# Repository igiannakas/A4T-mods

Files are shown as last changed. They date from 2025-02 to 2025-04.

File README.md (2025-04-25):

# WWG2 Mods for the A4T toolhead and filament cutter
This is my collection of mods for the A4T Toolhead (developed by Armchair-Heavy-Industries) cutter developed by SouthAsh1 and WWG2 (Wrist Watch G2) extruder developed by tetsu97 and modified by bythorsthunder to include a dual filament sensor. 

**Project source links below:**
1. https://github.com/Armchair-Heavy-Industries/A4T
2. https://github.com/bythorsthunder/Voron_Mods/tree/main/Wristwatch_G2_Dual_Filament_Sensor
3. https://github.com/SouthAsh1/A4T-AFC

All licenses are carried over from their respective creators. License information available in the links above.



# Modifications overview and rationale:
During my use of the A4T toolhead together with the southash1 developed filament cutter and Wrist Watch G2 extruder I've come across the following areas for improvement:

1. **Filament path diameter:** The WWG2 filament path was hexagonal, which while OK in principle, is "looser" than the latest circular filament path implemented in the G2E extruder by JaredC01. **Specifically the hexagonal path is up to 2.54mm in diameter vs. 2.1mm in the latest G2E extruder release.** This results in the filament path not being as constrained, which resulted in observable deviations in the PA value between G2E and WWG2. A cross sectional image of the revised filament path can be found below:


2. **WWG2 Filament entry point:** The WWG2 mod to include the dual filament sensors results in a **very thin wall between the upper ball bearing and the filament path** and entry point. This results in the filament path deforming when printed. In addition, the filament entry path has a **very shallow taper** where the filament enters the extruder from the top ECAS fitting. This results in slight filament collisions if the filament enters the extruder at a slight angle due to the filament twisting in the feeding tube or curling due to its natural spool curge. **These have been addressed in the modded design by elevating the ECAS mount point by 1mm and agressively tapering the filament entry path.** A cross sectional image of the revised filament entry path can be found below:


3. **WWG2 Filament exit and A4T direct filament entry path:** The dual filament sensor WWG2 had a very small recess to mount a bowden tube to the filament exit point. While this works well for toolheads that have a large bowden section after the extruder, when used in combination with the A4T AFC toolhead cutter, it resulted in **approximately 2-3mm of bowden tube needed to constrain the filament between the extruder and the A4T AFC extruder mount** adaptor. In addition, that bowden tube recess was again resulting in **thin walls on the WWG2** filament path that were deforming after printing. **Both of these have been addressed in the modded design by removing the bowden recess from both the WWG2 and the A4T extruder mount.** That small bowden tube was uncecessary and has been replaced with a coincident filament path, tapered at the entry of the A4T AFC to allow for proper filament guidance.


Please note that the M2 heatset is still needed to guide the filament through to the cutter and is fitted underneath the extruder adaptor filament path, here:


4. **WWG2 M3x20 and M3x25 screws mod:** The stock WWG2 main body requires M3x20 and M3x18 screws. I have discovered that the M3x20 is barely long enough to make it fully through the square nut. Also they do not extend all the way through to the holes underneath the nut, somewhat reducing stability. In this mod, the WWG2 front plate has been modified to allow for the use of M3x20 and M3x25 screws


5. **Reinforced blade holder:** While the stock design works well with PLA and ABS, when cutting fiber reinforced material (eg. PPA CF, PET CF) it tends to crack at infront of the lever bushing. The reinforced blade holder thickens that area allowing for more walls to be extruded, reducing the opportunity for cracks to appear.
 




6. **Updated WWG2 THB mount:** Updated THB mount for the XOL carriage with the rear support screw now able to be used again.


7. **Experimental: Updated cowling with enhanced support for the G2 extruder gearbox:** What I have noticed is that the extruder is now mounted a bit higher up compared to the stock A4T hotend. This allows the WWG2 extruder room to "vibrate" as the extruder rear plate is unsupported vs. the stock A4T where the extruder is supported by the housing of the A4T. I have updated the cowling to extend the rear mounting plate to support the underside of the WWG2 resulting in slightly improved IS results.

 

 

Please note that you will need to use supports in the slicer to print the extended support area. Apologies my CAD skills are not good enough to do this natively! Also as this is experimental, I have ony updated the Revo XOL cowling as that is the one my printer is using!



# Assembly tips
As the filament paths are now tigther than the original designs (2.1mm in diameter) you may need a 2mm drill bit to ream them out slightly if they are too tight for filament to pass through easily.

The **WWG2 extruder has shrinkage compensation for ABS like materials already built in** the base design, from which these mods are derived from. So in theory you shouldnt need to scale the parts.

The **A4T AFC parts do not have shrinkage compensation baked in the CAD**, so you'll need to apply your material shrinkage compensation as per the base design instructions.

Happy printing!

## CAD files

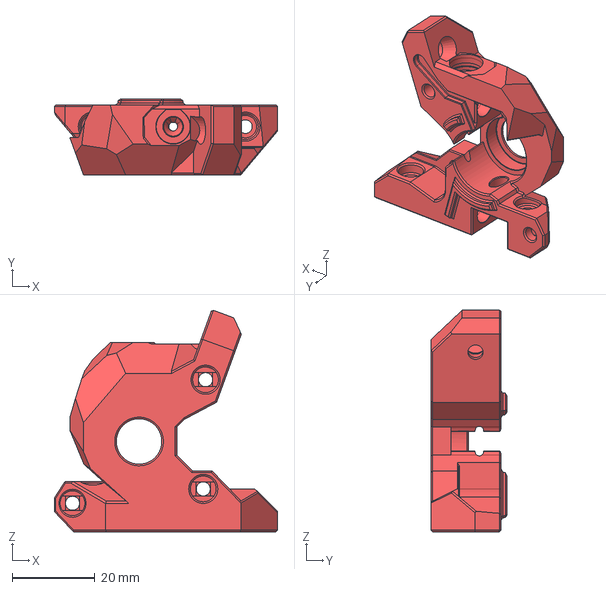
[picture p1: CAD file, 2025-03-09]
WWG2 Dual Filament Sensor/STEP/WWG2_DualFS Main body.step
54.1 x 18.4 x 53.7 mm

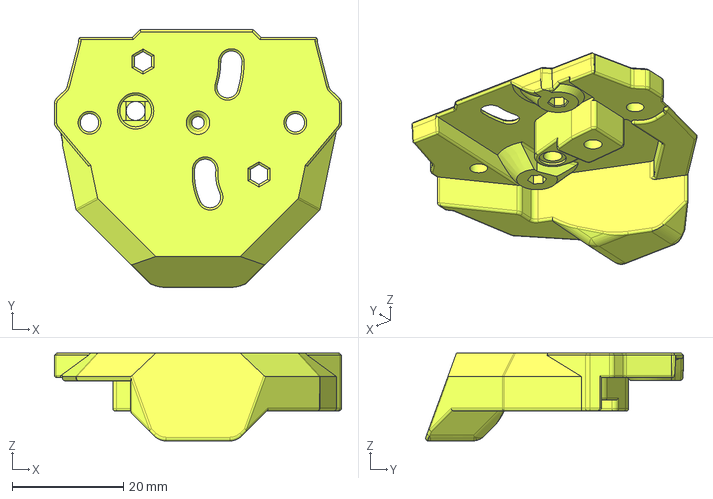
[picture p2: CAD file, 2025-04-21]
A4T - AFC mods/01. Extruder adapter - direct entry path/CAD/Extruder adapter - standard flow - direct entry path.step
51.6 x 46.3 x 15.8 mm

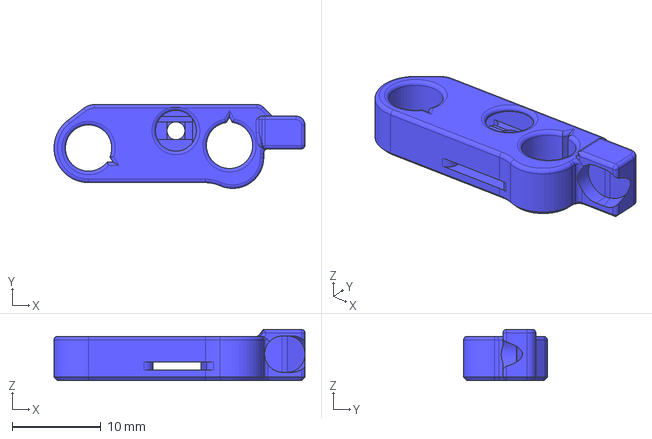
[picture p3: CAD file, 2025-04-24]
A4T - AFC mods/02. Reinforced blade holder/CAD/Blade Holder - reinforced.step
28.3 x 9.45 x 5.80 mm

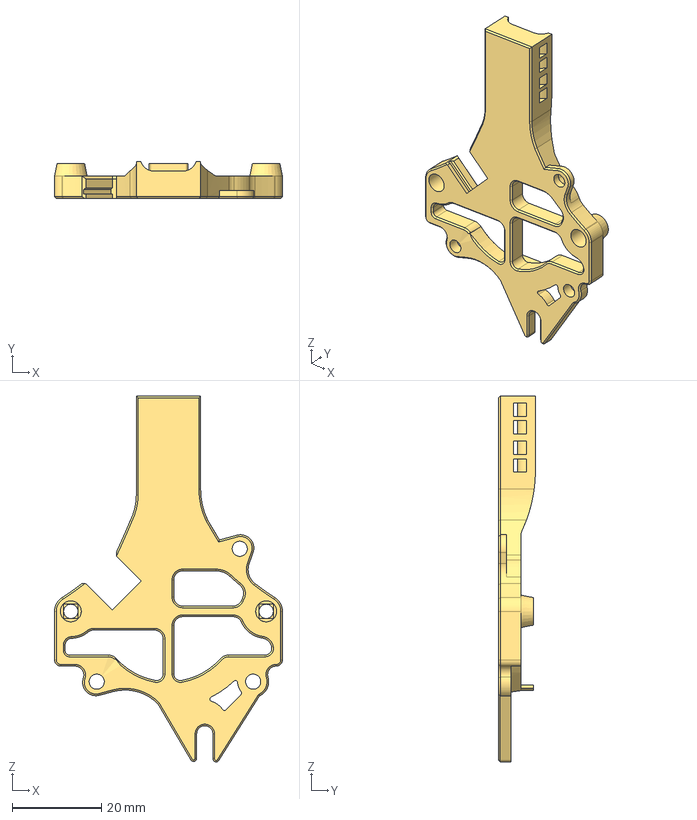
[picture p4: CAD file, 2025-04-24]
A4T - AFC mods/03. WWG2 THB Mount/CAD/THB Mount.step
51.2 x 8.26 x 82.1 mm

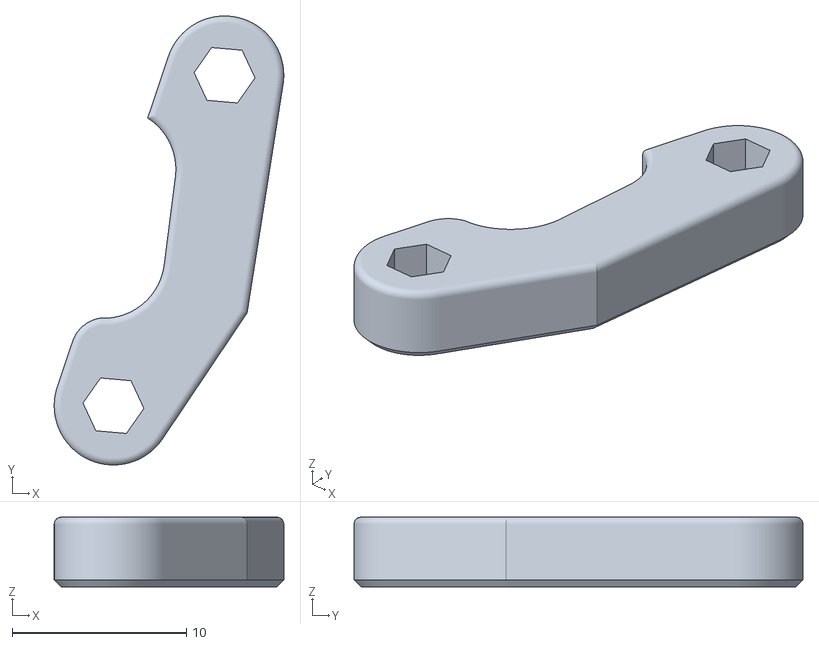
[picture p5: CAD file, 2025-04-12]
A4T - AFC mods/05. Remaining files from source repo/Link.stl
13.2 x 25.8 x 4.00

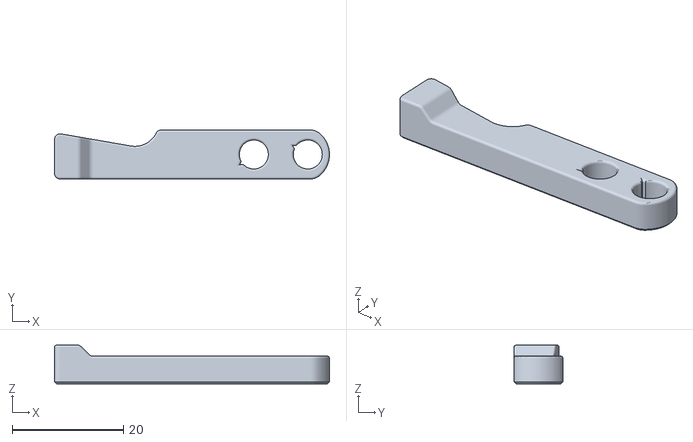
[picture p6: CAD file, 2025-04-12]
A4T - AFC mods/05. Remaining files from source repo/Cutter Bar.stl
49.4 x 8.80 x 7.00

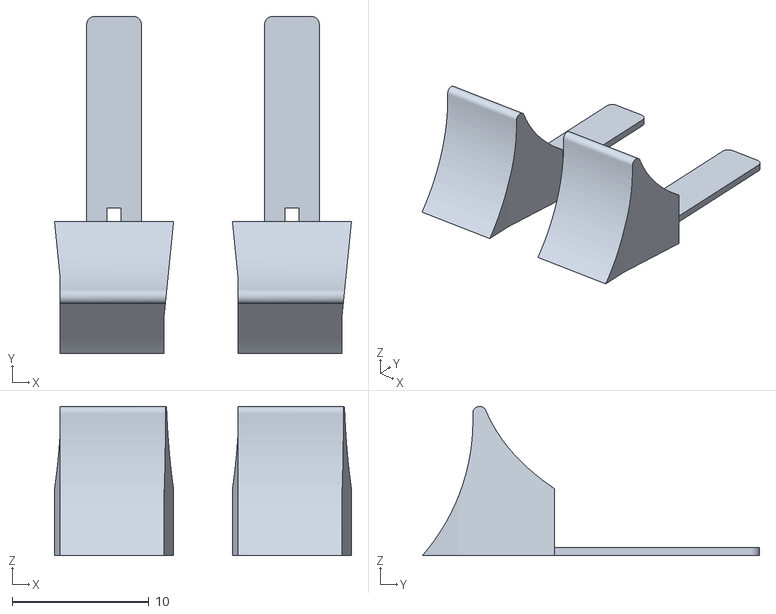
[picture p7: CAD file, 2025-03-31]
A4T - AFC mods/05. Remaining files from source repo/A4T Backflow Inhibitor [x2].stl
21.7 x 24.6 x 10.9

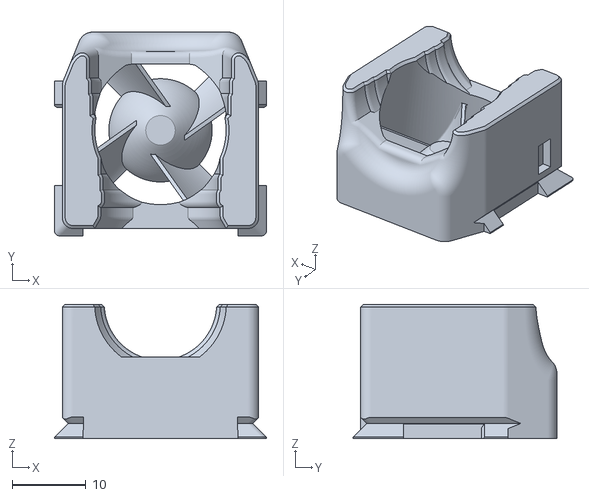
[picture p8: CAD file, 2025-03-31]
A4T - AFC mods/05. Remaining files from source repo/A4T HE Duct - Revo-Voron.stl
28.7 x 27.6 x 18.2

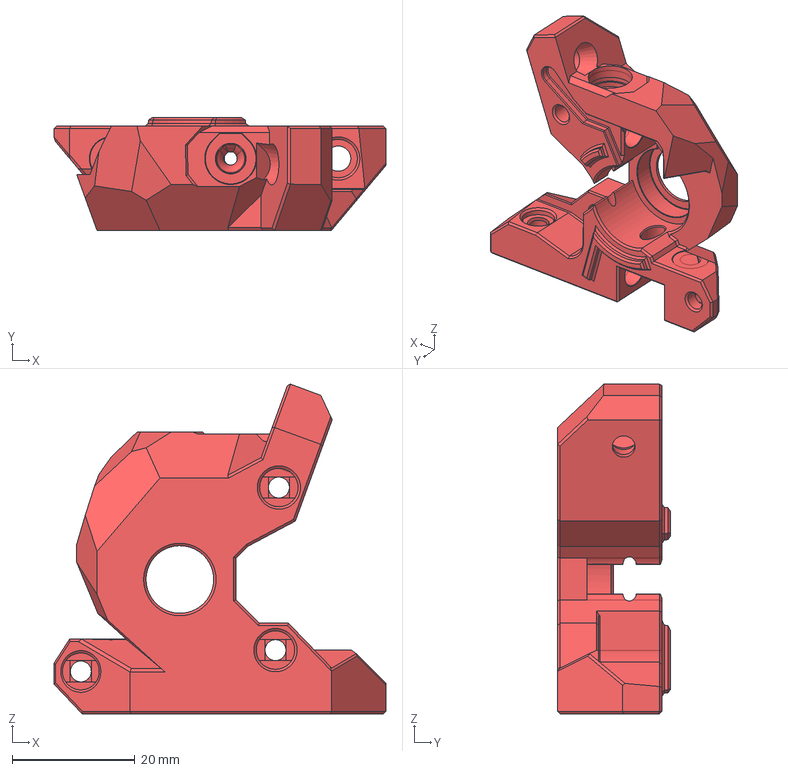
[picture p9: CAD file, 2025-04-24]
WWG2 Dual Filament Sensor/STEP/WWG2_DualFS Main body - longer screws (20 and 25mm).step
54.1 x 18.4 x 53.7 mm

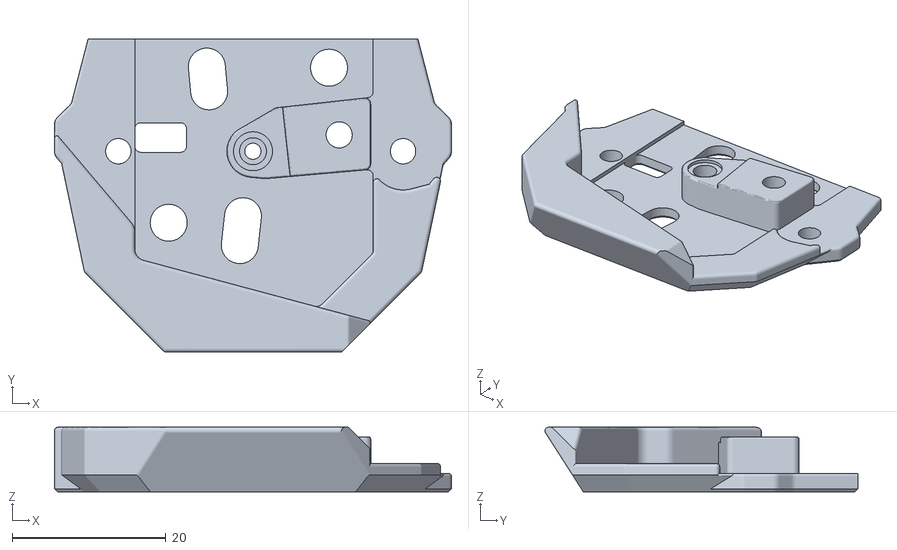
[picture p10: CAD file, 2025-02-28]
AFC screws version mods/A4T Extruder Mounting Plate/STL/A4T - Extruder Adapter UHF - Orbiter G2 - direct entry path.stl
51.6 x 40.7 x 8.41

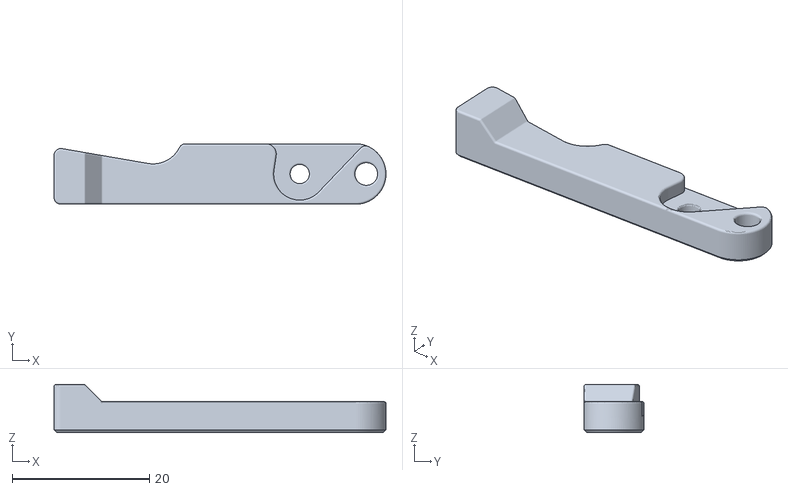
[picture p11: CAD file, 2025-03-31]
AFC screws version mods/Complete print project (Revo & WWG2)/Cutter Bar.stl
48.4 x 8.80 x 7.00

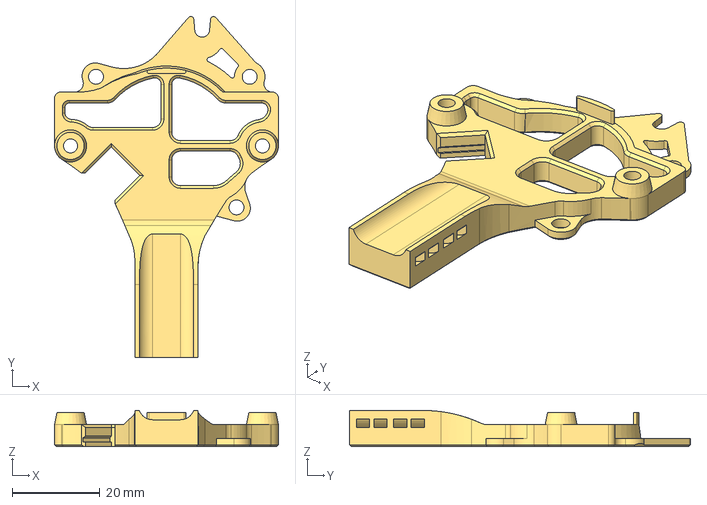
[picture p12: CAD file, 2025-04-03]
AFC screws version mods/THB Board Mount/STEP/A4T - THB Mount - WWG2 for AFC.step
51.2 x 77.9 x 8.26 mm

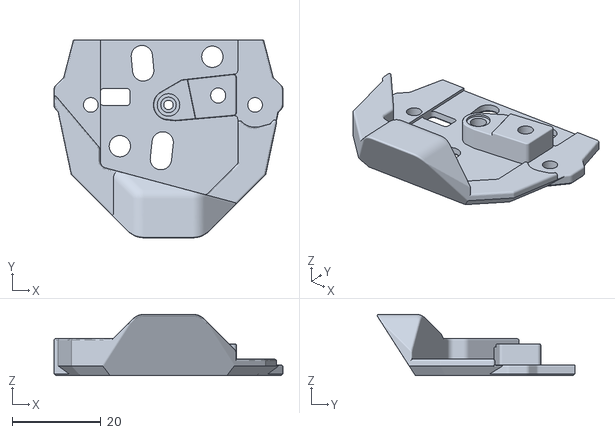
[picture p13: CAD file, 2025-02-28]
AFC screws version mods/A4T Extruder Mounting Plate/STL/A4T - Extruder Adapter - Orbiter G2 - direct entry path.stl
51.6 x 44.5 x 13.8

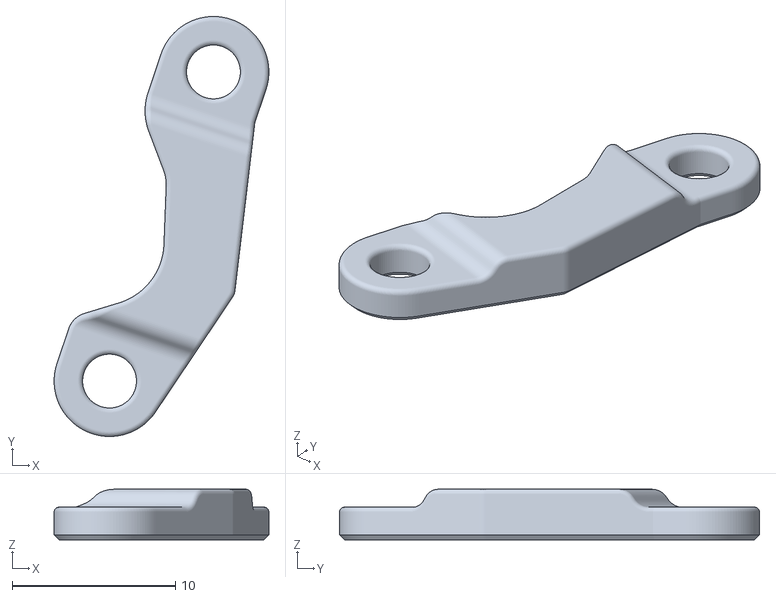
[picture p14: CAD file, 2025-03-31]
AFC screws version mods/Complete print project (Revo & WWG2)/Link.stl
13.2 x 25.8 x 3.10

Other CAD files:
WWG2 Dual Filament Sensor/STEP/WWG2_DualFS Main body modified.step
AFC screws version mods/Complete print project (Revo & WWG2)/Link shorter.stl
AFC screws version mods/Complete print project (Revo & WWG2)/Depressor Arm.stl
AFC screws version mods/Complete print project (Revo & WWG2)/Depressor Arm Base.stl
A4T - AFC mods/01. Extruder adapter - direct entry path/Extruder adapter - standard flow - direct entry path.stl
A4T - AFC mods/03. WWG2 THB Mount/THB Mount.stl
AFC screws version mods/Complete print project (Revo & WWG2)/A4T - THB Mount - WWG2.stl
AFC screws version mods/Complete print project (Revo & WWG2)/Blade Holder.stl
AFC screws version mods/Complete print project (Revo & WWG2)/WW_G2_DualFS_Rear_plate - from source repo.stl
AFC screws version mods/Complete print project (Revo & WWG2)/WW_G2_DualFS_Tension_Arm - from source repo.stl
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

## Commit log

2025-02-28 Initial Upload
    [A4T - Extruder Adapter - Orbiter G2 v3.stl, WWG2_DualFS Main body modified.step, WWG2_DualFS Main body modified.stl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]
2025-02-28 Uploaded direct entry path UHF mounts
    [A4T - Extruder Adapter - Orbiter G2 - direct entry path.stl, A4T - Extruder Adapter UHF - Orbiter G2 - direct entry path.stl]
2025-03-08 Tolerance adjustments for bearings and switch screws
    [WWG2_DualFS Main body modified.step, WWG2_DualFS Main body modified.stl]
2025-03-09 Increased top sensor switch clearance to reduce pressure on switch
    [WWG2_DualFS Main body modified - first draft.step, WWG2_DualFS Main body modified - first draft.stl, WWG2_DualFS Main body modified - increased bearing clearan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]
2025-03-31 A4T complete files inventory for Revo hotend
    [A4T - Extruder Adapter - Orbiter G2 - direct entry path.stl, A4T - THB Mount - WWG2.stl, A4T Backflow Inhibitor [x2].stl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]
2025-04-03 THB mount
    [A4T - THB Mount - WWG2 for AFC.step, A4T - THB Mount - WWG2 for AFC.stl]
2025-04-12 Pin version mods
    [Extruder adaptor.step, THB Mount.step]
2025-04-12 Reorganised files
    [A4T - Extruder Adapter - Orbiter G2 - direct entry path.stl, A4T - Extruder Adapter UHF - Orbiter G2 - direct entry path.stl, A4T - THB Mount - WWG2 for AFC.st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]
2025-04-21 Reorganised repo and updates
    [A4T - Extruder Adapter - Orbiter G2 - direct entry path.stl, A4T - Extruder Adapter UHF - Orbiter G2 - direct entry path.stl, A4T - THB Mount - WWG2 for AFC.st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]
2025-04-21 Improved clearances
    [Extruder adapter - standard flow - direct entry path.step]
2025-04-22 Updated entry paths
    [Extruder adapter - standard flow - direct entry path.step, Extruder adapter - standard flow - direct entry path.stl]
2025-04-24 Further mods testing
    [Blade Holder - 0.3mm back & reinforced region.step, Blade Holder.stl, THB Mount longer slot.step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]
2025-04-25 Updated with latest files
    [A4T Backflow Inhibitor [x2].stl, A4T HE Duct - Revo-Voron.stl, Blade Holder - 0.3mm back & reinforced region.step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]
2025-04-25 CAD model
